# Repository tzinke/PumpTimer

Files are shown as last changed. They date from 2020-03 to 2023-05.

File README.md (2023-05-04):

<p>A timer for my pool pump using a Raspberry Pi Zero W and a custom-made PCB.</p>

# Pool Pump Timer Instructions

<p>This device emits its own wi-fi network which will allow you to connect to the controller and set schedules and toggle the pump on/off.</p>

<p>The name of the network is PumpController, and the password is PumpController2803Pool</p>
  
<p>This network is NOT connected to the internet, so you'll probably want to deselect auto-connect for this network (otherwise your device might automatically hop on this network and not be connected to the internet). To control the device, you will also need to turn cell data off if connecting with a phone.</p>

<p>Once connected, open a browser and navigate to pumpcontroller.com. This will pull up the controller interface.</p>

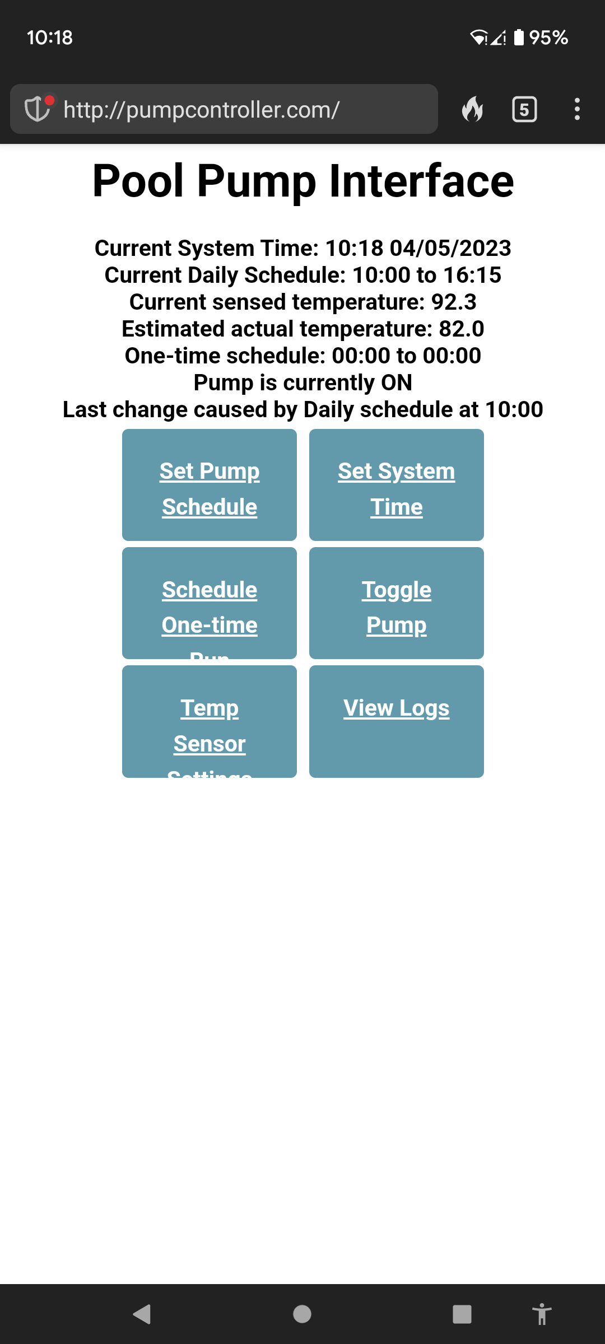
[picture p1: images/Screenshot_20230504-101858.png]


<p>Here, you can set a schedule to turn the pump on/off at the same time each day, set the on-board clock, set a "one-time run" (a schedule that will only execute a single time, after which the daily schedule will resume), toggle the pump on/off manually, and view logs from the last 3 months.
The on-board clock is very accurate with little drift, but it is not configured to automatically adjust for daylight savings.</p>

<p>The device is also configured to turn the pump on for at least 10 minutes if the temperature gets too close to 32F in order to prevent equipment damage from freezes.
The on-board temperature sensor isn't terribly accurate, so there is an adjustment factor that you can change to get it more accurate/modify the "freeze" threshold.</p>

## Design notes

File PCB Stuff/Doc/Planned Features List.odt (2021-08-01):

- 120VAC/60Hz to 5VDC converter
- Two relays – one for each phase of mains – with coils in parallel for simultaneous actuation
- Raspberry pi zero w as system controller
- Real-time clock w/ coin battery slot for accurate time keeping with or without main power
- Female headers for I2C, some GPIO for any future expansion (with pull-ups/impedance-matching resistors)
- Mounts to a raspberry pi zero w and to our old timer box (with 3D-printed mounting plate)

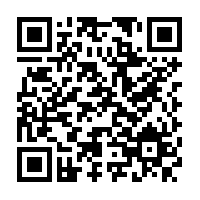
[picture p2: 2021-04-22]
images/medqr.png

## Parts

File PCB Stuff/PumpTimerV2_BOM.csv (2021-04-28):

Part | Value | Designator(s) | Count
RAC03-05SK | RAC03-05SK | PS1 | 1
ADW1205HLW | ADW1205HLW | K1 "K2" | 2
DMN67D7L | DMN67D7L | Q1 "Q2" | 2
BAV5004WS-7 | BAV5004WS-7 | D1 "D2" "D3" | 3
M20-9982046 | Conn_02x20_Odd_Even | J4 | 1
RX8900UA | RX8900UA | U1 | 1
CRGP0603F2K2 | 2k2 | R3 "R4" "R13" "R5" | 4
282856-2 | 282856-2 | J3 "J2" "J1" | 3
GMC31X5R107M10NT | 100u | C1 "C2" "C3" | 3
B4B-PH-SM4-TBT(LF)(SN) | B4B-PH-SM4-TBT(LF)(SN) | J6 | 1
ERJ-PA3J103V | 10k | R1 "R2" | 2
SML-D12U1WT86 | LED | D4 | 1
CRGCQ0603F330R | 330 | R14 | 1
50M025045G008 | 2.75mm | H1" "H3" "H5" "H6" "H4" "H2" | 6
TL3305AF160QG | TL3305AF160QG | SW1 | 1
LMK107BJ106MALTD | 10u | C4 | 1

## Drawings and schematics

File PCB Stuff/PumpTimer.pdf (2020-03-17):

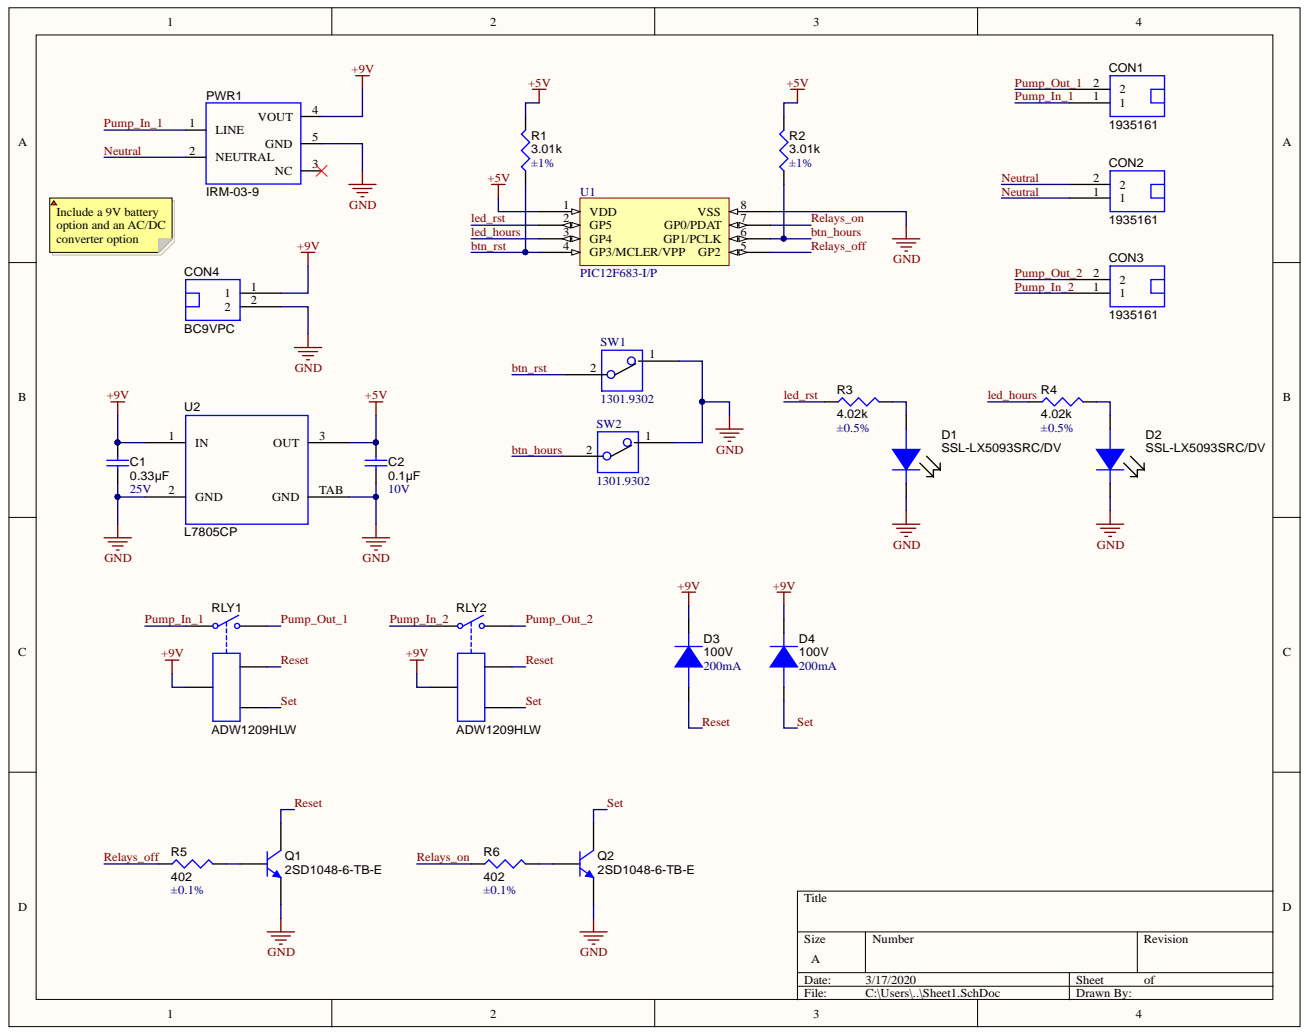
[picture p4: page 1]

Include a 9V battery
option and an AC/DC
converter option

GP5 2 GP4 3 | Relays_on

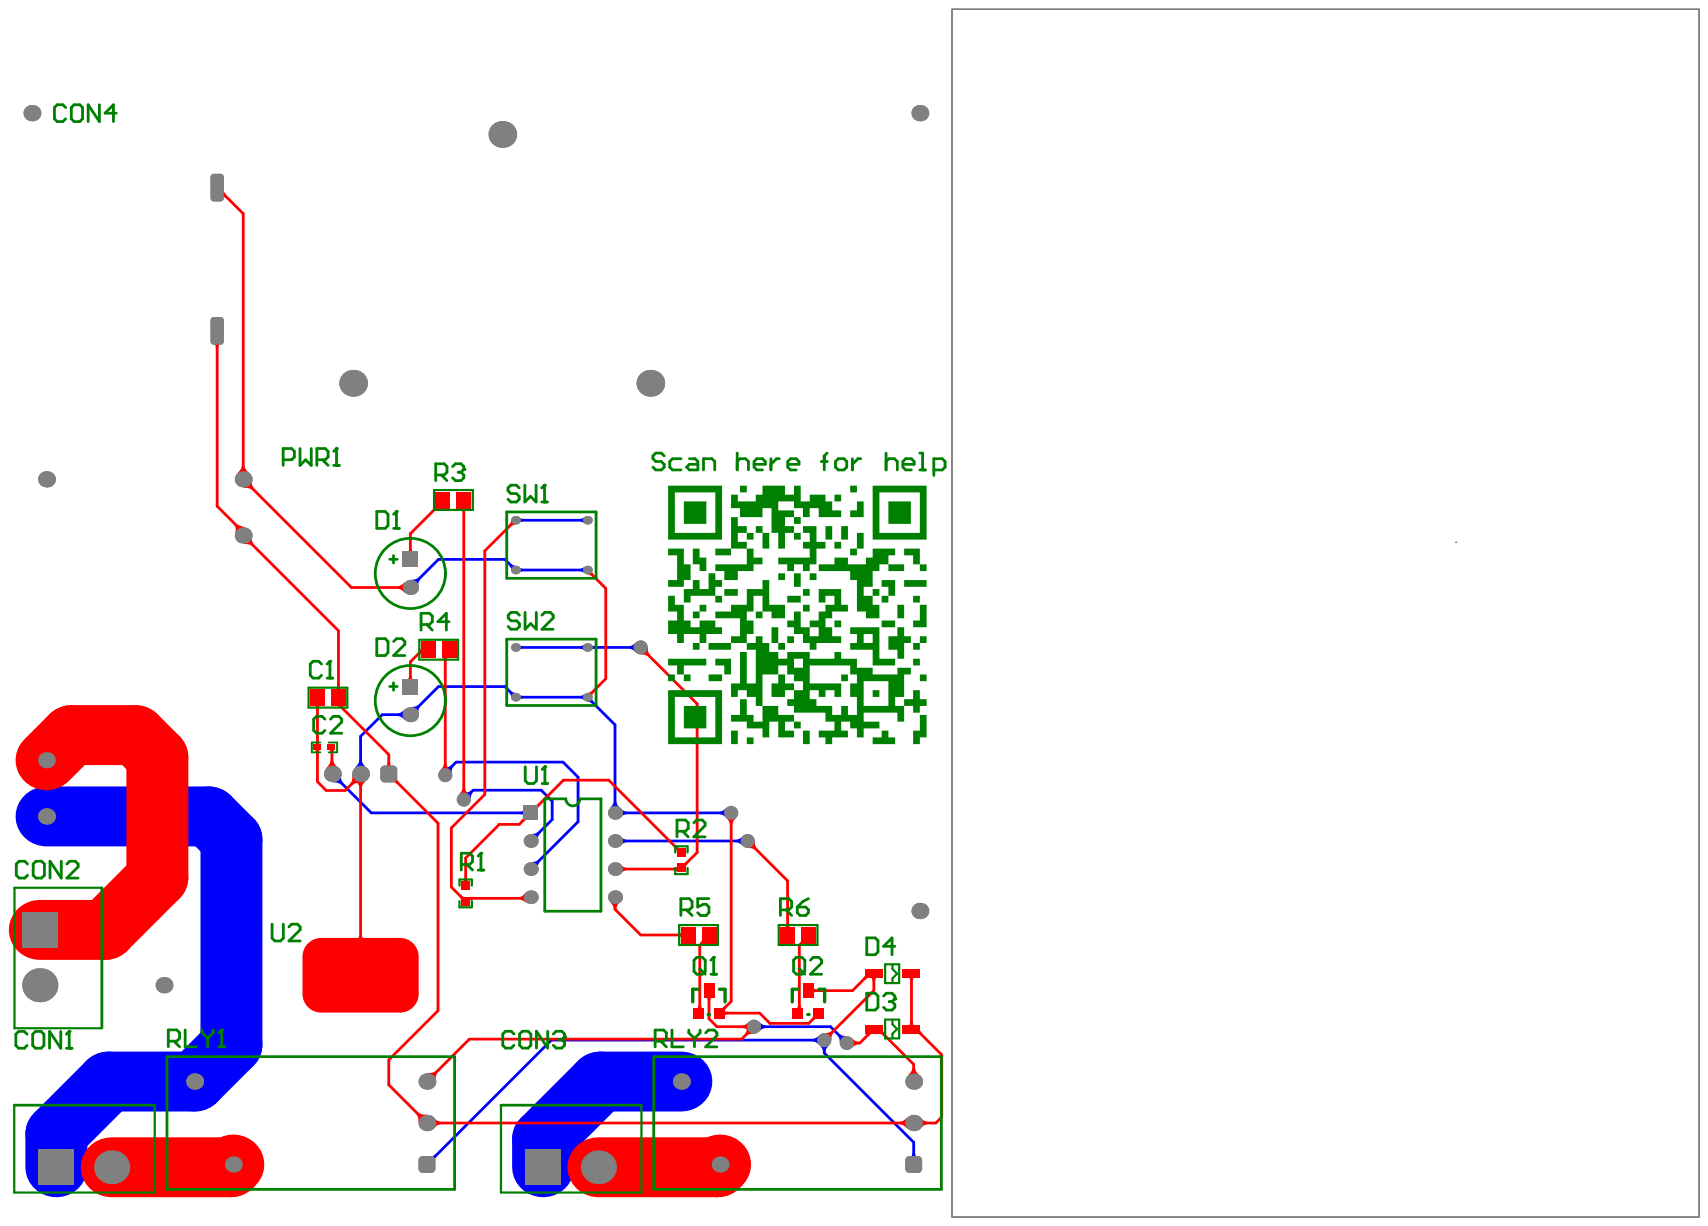
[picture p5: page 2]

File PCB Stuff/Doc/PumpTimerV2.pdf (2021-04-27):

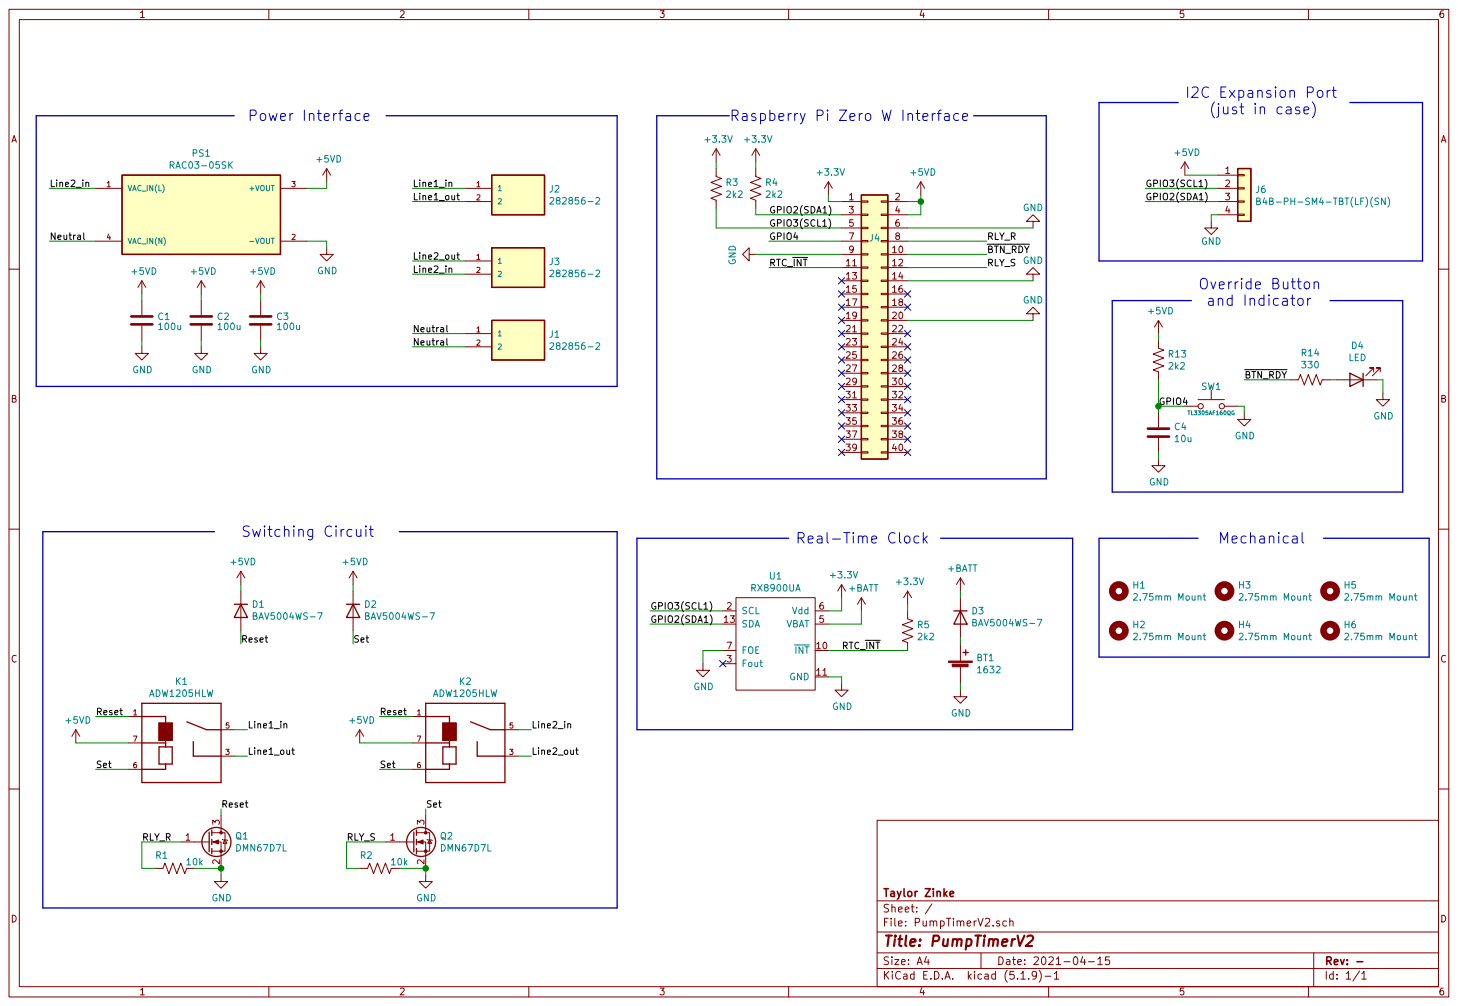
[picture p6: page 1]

J6B4B-PH-SM4-TBT(LF)(SN) GND

File: PumpTimerV2.sch Sheet: / Taylor Zinke GND

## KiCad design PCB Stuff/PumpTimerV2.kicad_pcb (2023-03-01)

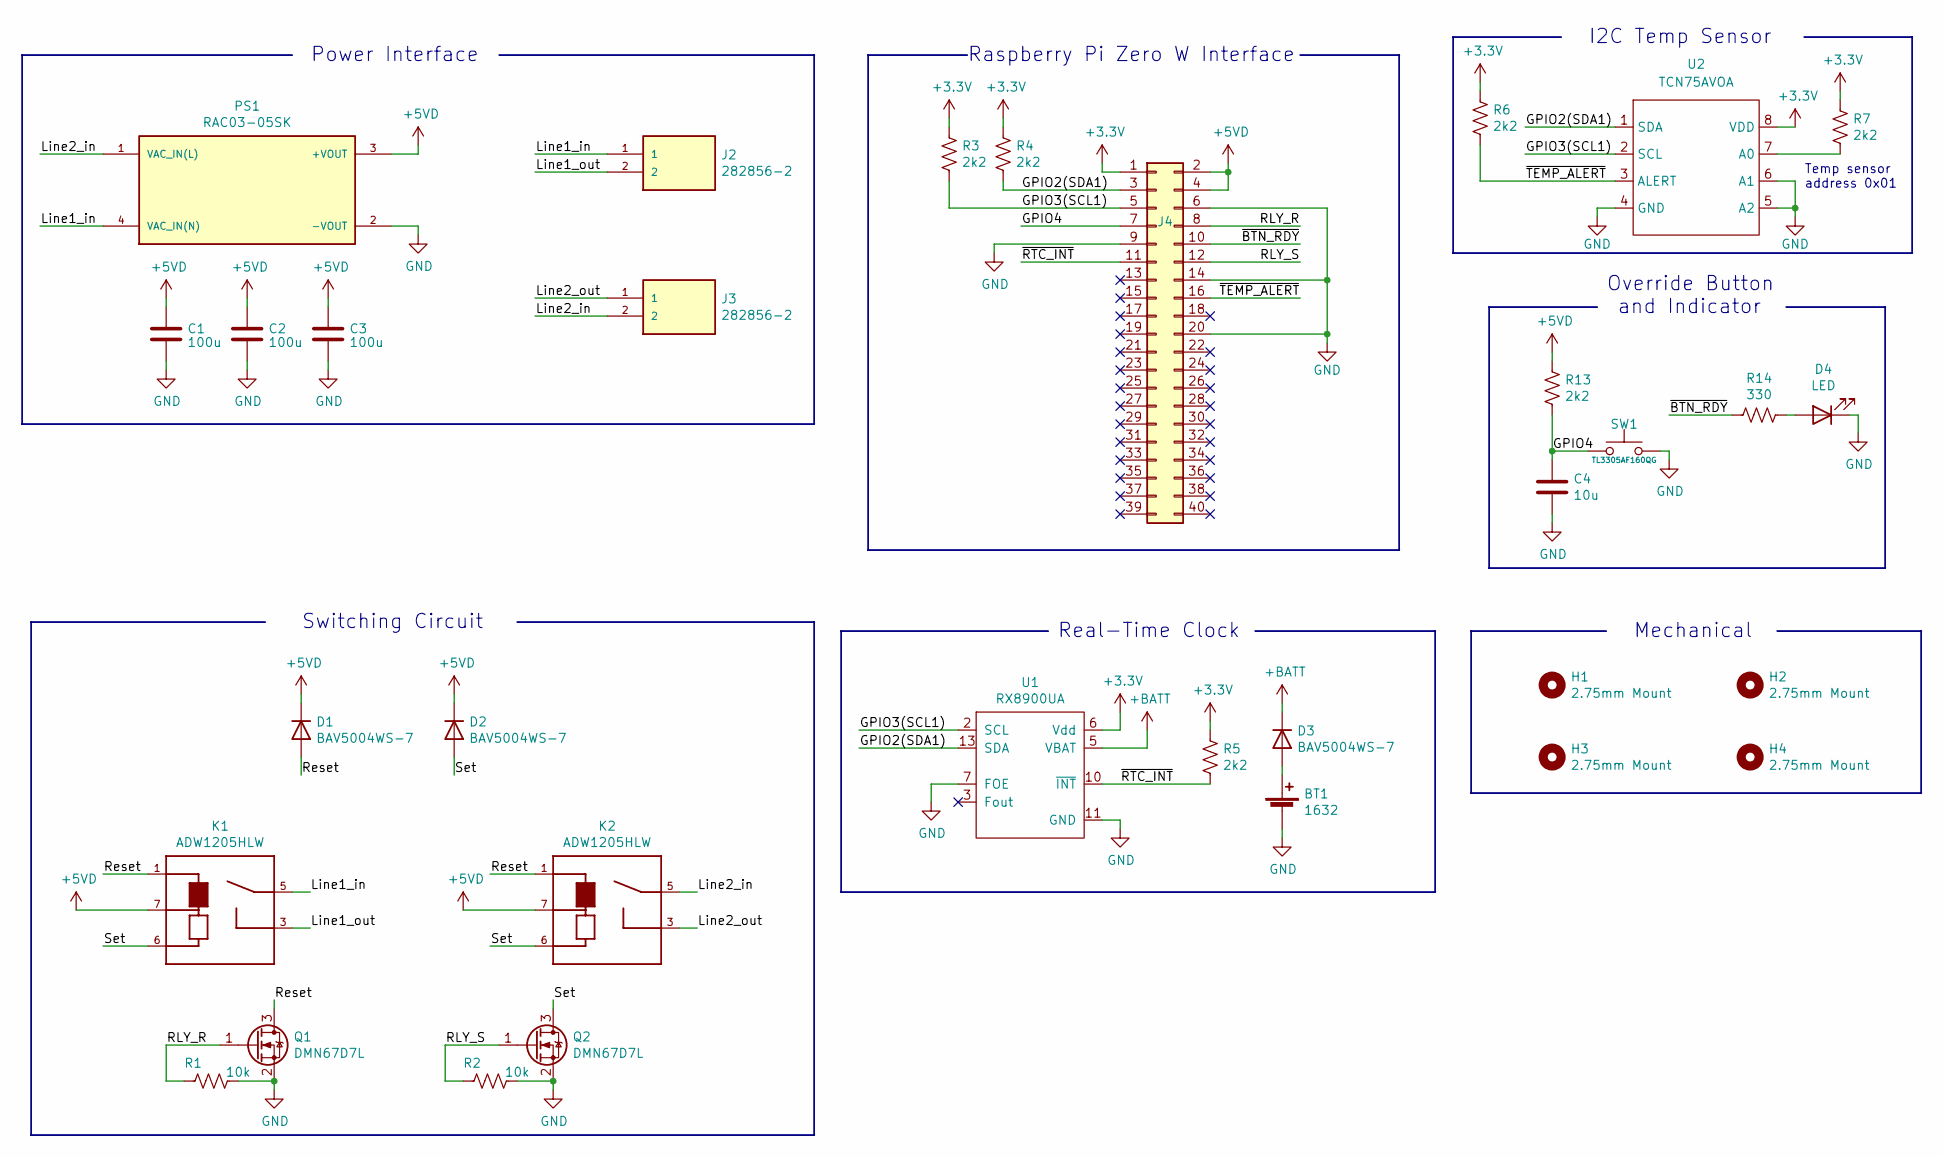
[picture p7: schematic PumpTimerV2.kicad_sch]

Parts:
BT1: 1632; Vertical_16mm_coin_holder; Part Keystone 1069
C1, C2, C3: 100u; C_1206_3216Metric_Pad1.33x1.80mm_HandSolder; Part GMC31X5R107M10NT
C4: 10u; C_0603_1608Metric_Pad1.08x0.95mm_HandSolder; Part LMK107BJ106MALTD
D1, D2, D3: BAV5004WS-7; D_SOD-323; Part BAV5004WS-7
D4: LED; LED_0603_1608Metric_Castellated; Part SML-D12U1WT86
H1, H2, H3, H4: 2.75mm Mount; MountingHole_2.7mm_M2.5; Part 50M025045G008
J2, J3: 282856-2; TE_282856-2; Part 282856-2
J4: Conn_02x20_Odd_Even; PinHeader_2x20_P2.54mm_Vertical; Part M20-9982046
K1, K2: ADW1205HLW; RELAY_ADW1205HLW; Part ADW1205HLW
PS1: RAC03-05SK; Part RAC03-05SK
Q1, Q2: DMN67D7L; SOT-23; Part DMN67D7L
R1, R2: 10k; R_0603_1608Metric_Pad0.98x0.95mm_HandSolder; Part ERJ-PA3J103V
R3, R4, R5, R6, R7, R13: 2k2; R_0603_1608Metric_Pad0.98x0.95mm_HandSolder; Part CRGP0603F2K2
R14: 330; R_0603_1608Metric_Pad0.98x0.95mm_HandSolder; Part CRGCQ0603F330R
SW1: TL3305AF160QG; Part TL3305AF160QG
U1: RX8900UA; SOP-14_127P780x200; Part RX8900UA
U2: TCN75AVOA; SOIC-8_3.9x4.9mm_P1.27mm

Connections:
+3V3: J4.1, R3.1, R4.1, R5.1, R6.1, R7.1, U1.6 (Vdd), U2.8 (VDD)
+5VD: C1.1, C2.1, C3.1, D1.2 (K), D2.2 (K), J4.2, J4.4, K1.7, K2.7, PS1.3 (+VOUT), R13.1
+BATT: D3.2 (K), U1.5 (VBAT)
/GPIO2(SDA1): J4.3, R4.2, U1.13 (SDA), U2.1 (SDA)
/GPIO3(SCL1): J4.5, R3.2, U1.2 (SCL), U2.2 (SCL)
/GPIO4: C4.1, J4.7, R13.2, SW1.1
/Line1_in: J2.1, K1.5, PS1.4 (VAC_IN(N))
/Line1_out: J2.2, K1.3
/Line2_in: J3.2, K2.5, PS1.1 (VAC_IN(L))
/Line2_out: J3.1, K2.3
/RLY_R: J4.8, Q1.1 (G), R1.2
/RLY_S: J4.12, Q2.1 (G), R2.2
/Reset: D1.1 (A), K1.1, K2.1, Q1.3 (D)
/Set: D2.1 (A), K1.6, K2.6, Q2.3 (D)
/~BTN_RDY: J4.10, R14.2
/~RTC_INT: J4.11, R5.2, U1.10 (~INT)
/~TEMP_ALERT: J4.16, R6.2, U2.3 (ALERT)
GND: BT1.NEG (-), C1.2, C2.2, C3.2, C4.2, D4.1 (K), J4.6, J4.9, J4.14, J4.20, PS1.2 (-VOUT), Q1.2 (S), Q2.2 (S), R1.1, R2.1, SW1.2, U1.7 (FOE), U1.11 (GND), U2.4 (GND), U2.5 (A2), U2.6 (A1)
unnamed: BT1.POS (+), D3.1 (A)
unnamed: D4.2 (A), R14.1
unnamed: R7.2, U2.7 (A0)

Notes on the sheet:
Override Button and Indicator
Mechanical
Switching Circuit
I2C Temp Sensor
Raspberry Pi Zero W Interface
Power Interface
Real-Time Clock
Temp sensor address 0x01

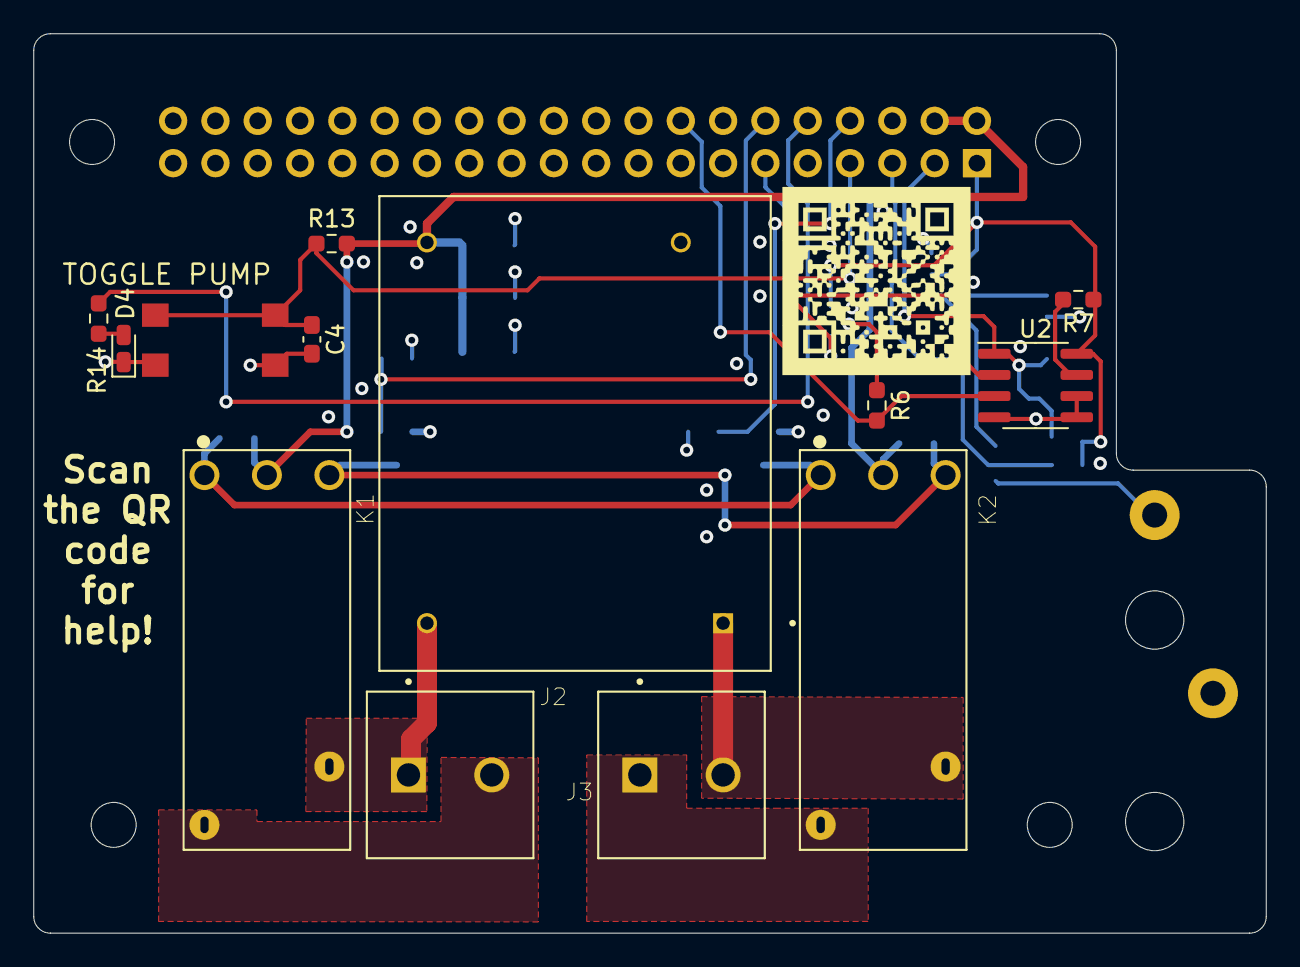
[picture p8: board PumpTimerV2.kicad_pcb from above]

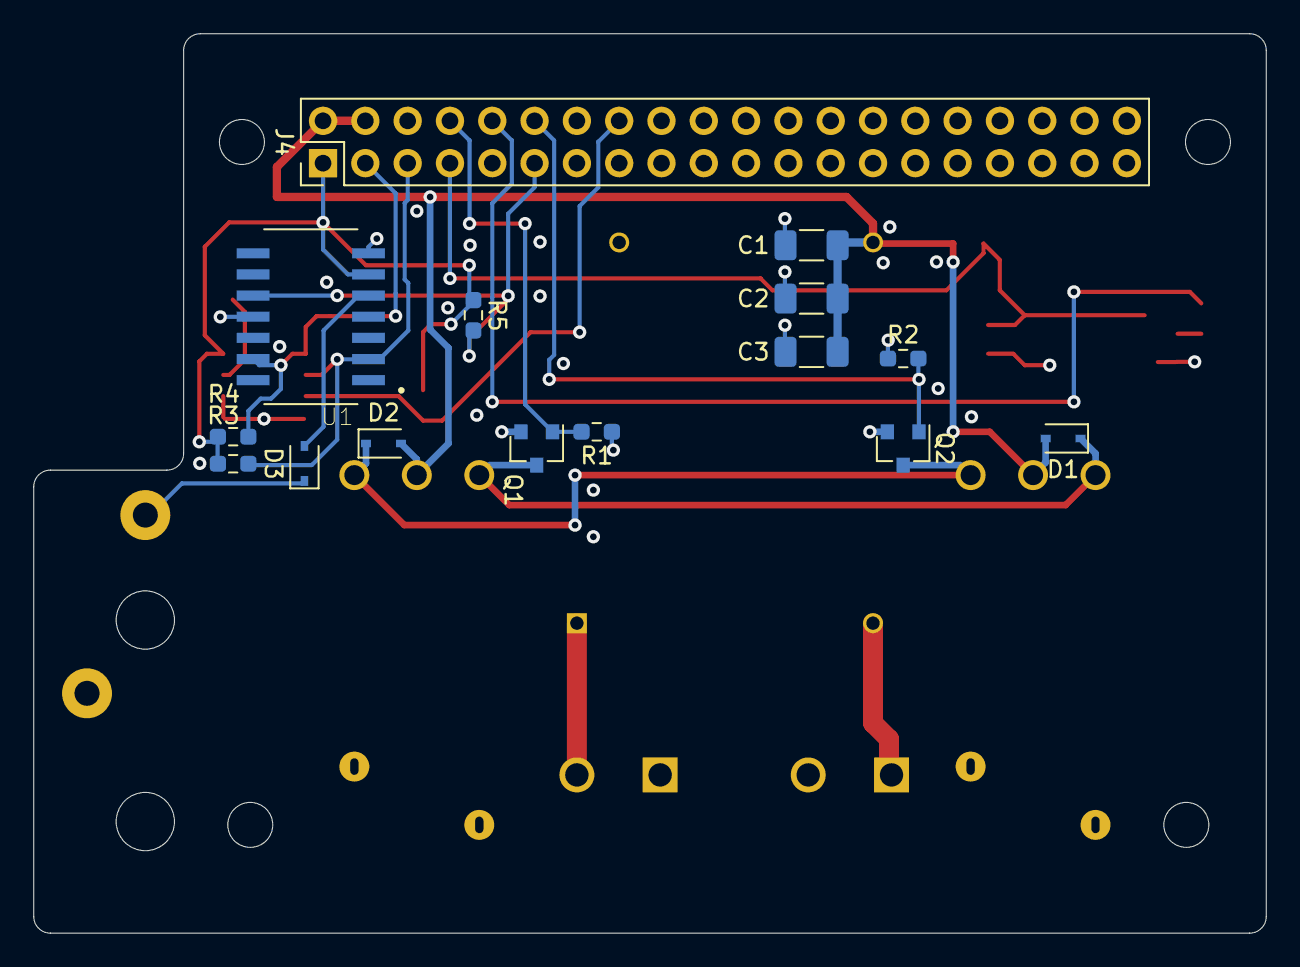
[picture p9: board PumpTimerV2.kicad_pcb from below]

Board: 4 copper layers, 74.0 x 54.0 mm, 33 parts (15 on the bottom side), 21 nets.

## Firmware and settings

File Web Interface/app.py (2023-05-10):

#!/usr/bin/python3

'''
app.py

Description
-----------
These functions are executed when requested by a client connected in a web browser to the address/port defined in this script.

Functions Defined
------------------
Function: top-level description
    Parameters
    Returns: Data type + description

set_schedule:

set_one_time:

set_time:

toggle_pump:

fetch_log:

Change Log
----------
27 Apr 2023 - Temp sensor operations added.

'''

##################################################################################################
# # Imports
##################################################################################################

import glob, os
import time
import smbus
import datetime
import subprocess
from flask import Flask, render_template, request, send_file
import RPi.GPIO as GPIO
from threading import Timer, Lock
from enum import Enum

##################################################################################################
# # Global Variables
##################################################################################################

# Define the address and port this server will run on
ip = "192.168.15.1"
server_port = 80

# Schedule and log file paths
# Schedule is written to file so the timer can resume
#   the schedule and temp offset (init data) in case of power outage
#   One-time schedules will be lost in power outage
initialization_data_path = "./static/initialization_data"
log_dir = "./static/logs/"
log_recovery = "./static/logRecovery"
log_path = '' # Will get set to current date
current_day = 0
class PumpState(Enum):
    DAILY_SCHED_ON = 1
    ONE_TIME_RUN_ON = 2
    WEB_TOGGLE_ON = 3
    BUTTON_ON = 4
    FREEZE_PROTECTION_ON = 5
    OFF = 6
class MonthNames(Enum):
    Jan = 1
    Feb = 2
    Mar = 3
    Apr = 4
    May = 5
    June = 6
    July = 7
    Aug = 8
    Sep = 9
    Oct = 10
    Nov = 11
    Dec = 12

# State variables
current_pump_state = PumpState.OFF
pump_one_time_run = False
lastEvent = "None" # Possible values: "button", "daily schedule", "one-time schedule", "pressure failure"
lastEventTime = 0
general_cooldown = 0 # This is to prevent overly-frequent pump-state changes. Each change will incur a 3s general_cooldown
freeze_protection_cooldown = False # This is to prevent overly-frequent pump-state changes. If the freeze-protection changes pump state, it will stay so for at least 10 minutes
mutex = Lock() # This is to prevent unwanted interactions between timer and button events
sensor_temp = 0
temp_offset = 0
adjusted_temp = 0
freeze_protection_threshold = 33.5
temp_sensor_failure = False

# Schedule variables
currtime = -1
sched_on = 0
sched_off = 0
one_time_on = 0
one_time_off = 0
# Don't want one-time-run settings to remain active after completing
one_time_run_pending = 0 #0 = not pending; 1 = pending

# I2C variables
bus = smbus.SMBus(1)
rtc_addr = 0x32
temp_sensor_addr = 0x49 #todo might need to shift left 1 bit

sensors = {
    1 : {'name' : 'Time', 'data' : 'None'},
    2 : {'name' : 'Temp', 'data' : 'None'}
}

app = Flask(__name__)

##################################################################################################
# # Function Definitions/Client Routing
##################################################################################################

def rtc_set(time_string):
    """
    Description
    -----------
    This function writes to the registers of the RTC

    Parameters
    ----------
    time_string: String with the current 24-hour time formatted as
        "yyyy mm dd HH MM SS"

    Returns
    -------
    None

    Examples
    --------

    Change Log
    ----------

    Notes
    -----
    """
    currtime = datetime.datetime.strptime(time_string, "%Y %m %d %H %M %S")
    yy = currtime.year - 2000

    second= (int(currtime.second /10) * 16) + (currtime.second % 10)
    minute = (int(currtime.minute /10) * 16) + (currtime.minute % 10)
    hour = (int(currtime.hour /10) * 16) + (currtime.hour % 10)
    day = (int(currtime.day /10) * 16) + (currtime.day % 10)
    month = (int(currtime.month /10) * 16) + (currtime.month % 10)
    year = (int(yy /10) * 16) + (yy % 10)

    bus.write_i2c_block_data(rtc_addr, 0, [second, minute, hour, 1, day, month, year])

def rtc_get():
    """
    Description
    -----------
    This function reads from the registers of the RTC and sets the system time
        accordingly.

    Parameters
    ----------
    None

    Returns
    -------
    A list containing the current RTC setting

    Examples
    --------

    Change Log
    ----------

    Notes
    -----
    """
    regs = bus.read_i2c_block_data(rtc_addr, 0, 7)

    seconds = "%d" % ((int(regs[0]/16) * 10) + (regs[0] % 16))
    if int(seconds) < 10:
        seconds = "0" + seconds
    minutes = "%d" % ((int(regs[1]/16) * 10) + (regs[1] % 16))
    if int(minutes) < 10:
         minutes = "0" + minutes
    hours = "%d" % ((int(regs[2]/16) * 10) + (regs[2] % 16))
    if int(hours) < 10:
         hours = "0" + hours
    day = "%d" % ((int(regs[4]/16) * 10) + (regs[4] % 16))
    if int(day) < 10:
         day = "0" + day
    month = "%d" % ((int(regs[5]/16) * 10) + (regs[5] % 16))
    if int(month) < 10:
         month = "0" + month
    year = "%d" % ((int(regs[6]/16) * 10) + (regs[6] % 16))
    if int(year) < 10:
         year = "0" + year

    return [seconds, minutes, hours, day, month, year]

def temp_get():
    bytes = bus.read_i2c_block_data(temp_sensor_addr, 0, 2)
    temp = int(bytes[0] << 8) + int(bytes[1])
    temp = float(temp * 0.00390625)
    return temp 

def updateLog():
    with open(log_path, 'a') as log:
        log.write("%s turned pump %s at %s\n" % (lastEvent, ("OFF" if (current_pump_state is PumpState.OFF) else "ON"), lastEventTime))
        log.write("Sensed temp: %7.1f\t, Adjusted temp: %7.1f\n" % (sensor_temp, adjusted_temp))

def startPump(source):
    global current_pump_state, general_cooldown
    if general_cooldown is 0:
        # GPIO18 high for 15ms
        GPIO.output(18, 1)
        time.sleep(0.015)
        GPIO.output(18, 0)
        current_pump_state = source
        print("Pump started by %s" % source.name)

        GPIO.output(15,1)
        general_cooldown = 1
        Timer(3, general_cooldown_counter, ()).start()

def stopPump():
    global current_pump_state, general_cooldown
    if general_cooldown is 0:
        # GPIO14 high for 15ms
        GPIO.output(14, 1)
        time.sleep(0.015)
        GPIO.output(14, 0)
        current_pump_state = PumpState.OFF

        GPIO.output(15,1)
        general_cooldown = 1
        Timer(3, general_cooldown_counter, ()).start()

def toggle_pump(button):
    global lastEvent, lastEventTime, mutex

    mutex.acquire()
    if (current_pump_state is PumpState.OFF):
        startPump(PumpState.BUTTON_ON)
    else:
        stopPump()

    mutex.release()
    lastEvent = "Button"
    lastEventTime = "%s:%s" % (sensors[0][2], sensors[0][1])
    updateLog()

def general_cooldown_counter():
    global general_cooldown
    general_cooldown = 0
    GPIO.output(15,0)
    
def freeze_protection_cooldown_counter():
    global freeze_protection_cooldown
    freeze_protection_cooldown = False

def application_tick():
    global mutex, sensors, lastEvent, lastEventTime, currtime, sensor_temp, adjusted_temp, one_time_on, one_time_off, one_time_run_pending, current_day, log_path, freeze_protection_cooldown
    # Check if the current time matches sched_on, sched_off, one_time_on, or one_time_off
    #   and change pump state if necessary
    sensors[0] = rtc_get()
    currtime = int(sensors[0][2])*100 + int(sensors[0][1])
    
    if not temp_sensor_failure:
        sensors[1] = temp_get()
        sensor_temp = (sensors[1] * 1.8) + 32.0 
        adjusted_temp = sensor_temp + temp_offset
        print("%7.1f + %7.1f = %7.1f" % (sensor_temp, temp_offset, adjusted_temp))

    drift_correction = 60 - int(sensors[0][0]) #Subtract out the seconds from timer delay so this happens on the minute
    print("Drift correction: %d" % drift_correction)

    mutex.acquire(blocking=False)
    if mutex.locked():
        if (adjusted_temp <= freeze_protection_threshold): # Risking freeze conditions!
            print("Freeze condition detected! PumpState is %s, freeze prot cooldown is %d" % (current_pump_state.name, freeze_protection_cooldown))
            if (current_pump_state is PumpState.OFF) and (freeze_protection_cooldown is False): # Pump is not on, and the cooldown period has ended
                print("In freeze protect block")
                startPump(PumpState.FREEZE_PROTECTION_ON)
                freeze_protection_cooldown = True
                Timer(10 * 60, freeze_protection_cooldown_counter, ()).start()
                lastEvent = "Freeze protection on"
                lastEventTime = "%s:%s" % (sensors[0][2], sensors[0][1])
                updateLog()

        else:
            desired_pump_state = current_pump_state
            lastEventBuffer = 0
            source = PumpState.OFF

            if (current_pump_state is PumpState.FREEZE_PROTECTION_ON) and (freeze_protection_cooldown is False): # Pump is on due to freeze protection, and the cooldown poweriod has ended
                desired_pump_state = 0 # Want to turn the pump off. Schedules can override this.
                lastEventBuffer = "Freeze protection off"

            # Check one-time schedule first to give preference to one-time schedules
            # Check off-times first so time-collisions will result in pump state OFF
            if one_time_run_pending is 1:
                if currtime == one_time_off:
                    desired_pump_state = 0
                    one_time_run_pending = 0 # one-time-run schedule finished
                    one_time_on = one_time_off = 0
                    lastEventBuffer = "One-time schedule"
                elif currtime == one_time_on:
                    desired_pump_state = 1
                    source = PumpState.ONE_TIME_RUN_ON
                    lastEventBuffer = "One-time schedule"
            else:
                if currtime == sched_off:
                    desired_pump_state = 0
                    lastEventBuffer = "Daily schedule"
                elif currtime == sched_on:
                    desired_pump_state = 1
                    source = PumpState.DAILY_SCHED_ON
                    lastEventBuffer = "Daily schedule"
                    
            if (desired_pump_state is 1) and (current_pump_state is PumpState.OFF):
                startPump(source)
                lastEvent = lastEventBuffer
                lastEventTime = "%s:%s" % (sensors[0][2], sensors[0][1])
                updateLog()
            elif (desired_pump_state is 0) and (not (current_pump_state is PumpState.OFF)):
                stopPump()
                lastEvent = lastEventBuffer
                lastEventTime = "%s:%s" % (sensors[0][2], sensors[0][1])
                updateLog()

        mutex.release()

    timer_clock = Timer(drift_correction, application_tick, ())
    timer_clock.start()

    if current_day is not int(sensors[0][3]):
        current_day = int(sensors[0][3])
        log_path = "%s%s_%s_%s" % (log_dir, sensors[0][3], sensors[0][4], sensors[0][5])

        with open(log_path, 'a') as newlog:
            newlog.write("Starting log at %s\n" % currtime)
        with open(log_recovery, 'w') as newlogrec:
            newlogrec.write("%d\n" % current_day)
            newlogrec.write(log_path)

        try:
            # Delete log from 3 months ago to remove clutter (who needs such an old log?)
            month = int(sensors[0][4])
            if month < 4:
                for f in glob.glob("%s%s_%02d*" % (log_dir, sensors[0][3], 9 + month)):
                    print("Attempting to remove log %s" % f)
                    os.remove(f)
            else:
                for f in glob.glob("%s%s_%02d*" % (log_dir, sensors[0][3], month - 3)):
                    print("Attempting to remove log %s" % f)
                    os.remove(f)
        except OSError: # Such log doesn't exist
            print("Failed to remove log!")
            pass

@app.route("/")
def main():
    """
    Description
    -----------
    This function gets called when the client navigates to "[serveraddress]/"
    (AKA the home page of the web app)

     Parameters
    ----------
    None

    Returns
    -------
    Renders the main.html page

    Examples
    --------

    Change Log
    ----------

    Notes
    -----
    """
    templateData = {
        'curr_time' : ("%s:%s %s %s 20%s" %  (sensors[0][2], sensors[0][1], sensors[0][3], MonthNames(int(sensors[0][4])).name, sensors[0][5])),
        'sensed_temp' : ("%4.1f" % sensor_temp),
        'estimated_temp' : ("%4.1f" % adjusted_temp),
        'sched_on' : ("%02d:%02d" % (int(sched_on/100), sched_on - (int(sched_on/100) * 100))),
        'sched_off' : ("%02d:%02d" % (int(sched_off/100), sched_off - (int(sched_off/100) * 100))),
        'once_on' : ("%02d:%02d" % (int(one_time_on/100), one_time_on - (int(one_time_on/100) * 100))),
        'once_off' : ("%02d:%02d" % (int(one_time_off/100), one_time_off - (int(one_time_off/100) * 100))),
        'last' : lastEvent,
        'lastEventTime' : lastEventTime,
        'pump_state' : ("Pump is currently OFF" if (current_pump_state is PumpState.OFF) else "Pump is currently ON")
    }
    # Pass the template data into the template main.html and return it to the user
    return render_template('main.html', **templateData)

@app.route("/setSchedule", methods=['GET', 'POST'])
def set_schedule():
    global sched_off, sched_on, lastEvent, lastEventTime
    if request.method == 'POST':
        on_time = request.form['new_on']

        if not on_time == '':
            strsplt = on_time.split(':')
            on_hh = int(strsplt[0])
            on_mm = int(strsplt[1])

            if (23 < on_hh) or (0 > on_hh):
                raise TypeError("HOUR: You must enter an integer between 0 and 23")
            elif(59 < on_mm) or (0 > on_mm):
                raise TypeError("MINUTE: You must enter an integer between 0 and 59")

            sched_on = (on_hh * 100) + on_mm

            with open(initialization_data_path, "r") as file:
                file.readline()
                old_off = int(file.readline())

            with open(initialization_data_path, "w") as file:
                file.write("%d\n" % sched_on)
                file.write("%d\n" % old_off)
                file.write("%5.1f\n" % temp_offset)
                file.write("%7.1f" % freeze_protection_threshold)

        off_time = request.form['new_off']

        if not off_time == '':
            strsplt = off_time.split(':')
            off_hh = int(strsplt[0])
            off_mm = int(strsplt[1])

            if (23 < off_hh) or (0 > off_hh):
                raise TypeError("HOUR: You must enter an integer between 0 and 23")
            elif(59 < off_mm) or (0 > off_mm):
                raise TypeError("MINUTE: You must enter an integer between 0 and 59")

            sched_off = (off_hh * 100) + off_mm

            with open(initialization_data_path, "r") as file:
                old_on = int(file.readline())

            with open(initialization_data_path, "w") as file:
                file.write("%d\n" % old_on)
                file.write("%d\n" % sched_off)
                file.write("%5.1f\n" % temp_offset)
                file.write("%7.1f" % freeze_protection_threshold)

        if (one_time_run_pending is 0):
            if sched_off < sched_on: # Wrap through midnight
                if (currtime >= sched_on) or (currtime < sched_off):
                    startPump(PumpState.DAILY_SCHED_ON)
                    print("Currtime >= sch on OR < sched_off -> pump on")
                    lastEvent = "Daily schedule"
                    lastEventTime = "%s:%s" % (sensors[0][2], sensors[0][1])
                    updateLog()
                elif not (current_pump_state is PumpState.OFF): # Outside new schedule time + pump is on
                    stopPump()
                    print("NOT currtime >= sch on OR < sched_off -> pump off")
                    lastEvent = "Daily schedule"
                    lastEventTime = "%s:%s" % (sensors[0][2], sensors[0][1])
                    updateLog()
            elif sched_off > sched_on:
                if (currtime >= sched_on) and (currtime < sched_off):
                    startPump(PumpState.DAILY_SCHED_ON)
                    print("Currtime >= sch on AND < sched_off -> pump on")
                    lastEvent = "Daily schedule"
                    lastEventTime = "%s:%s" % (sensors[0][2], sensors[0][1])
                    updateLog()
                elif not (current_pump_state is PumpState.OFF): # Outside new schedule time + pump is on
                    stopPump()
                    print("NOT currtime >= sch on AND < sched_off -> pump off")
                    lastEvent = "Daily schedule"
                    lastEventTime = "%s:%s" % (sensors[0][2], sensors[0][1])
                    updateLog()
            else: # sched_off is the same as sched_on
                lastEvent = "Daily schedule"
                lastEventTime = "%s:%s" % (sensors[0][2], sensors[0][1])
                stopPump()
                updateLog()

    templateData = {
        'curr_time' : ("%s:%s %s %s 20%s" %  (sensors[0][2], sensors[0][1], sensors[0][3], MonthNames(int(sensors[0][4])).name, sensors[0][5])),
        'curr_on' : ("%02d:%02d" % (int(sched_on/100), sched_on - (int(sched_on/100) * 100))),
        'curr_off' : ("%02d:%02d" % (int(sched_off/100), sched_off - (int(sched_off/100) * 100)))
    }

    return render_template('setSchedule.html', **templateData)

@app.route("/setOneTime", methods=['GET', 'POST'])
def set_one_time_run():
    global one_time_off, one_time_on, one_time_run_pending, lastEvent, lastEventTime
    if request.method == 'POST':
        try:
            strsplt = request.form['new_on'].split(':')
            on_hh = int(strsplt[0])
            on_mm = int(strsplt[1])

            strsplt = request.form['new_off'].split(':')
            off_hh = int(strsplt[0])
            off_mm = int(strsplt[1])

            if (23 < on_hh) or (23 < off_hh) or (0 > on_hh) or (0 > off_hh):
                raise TypeError("HOUR: You must enter an integer between 0 and 23")
            elif(59 < on_mm) or (59 < off_mm) or (0 > on_mm) or (0 > off_mm):
                raise TypeError("MINUTE: You must enter an integer between 0 and 59")

            one_time_on = (on_hh * 100) + on_mm
            one_time_off = (off_hh * 100) + off_mm

            print("Got one-time on:\t%d\nOne-time off:\t%d\n" % (one_time_on, one_time_off))

            one_time_run_pending = 1
            if one_time_off < one_time_on: # Wrap through midnight
                if (currtime >= one_time_on) or (currtime < one_time_off):
                    startPump(PumpState.ON_TIME_RUN_ON)
                    print("One-time schedule includes current time. Turning pump on\n")
                    lastEvent = "One-time schedule"
                    lastEventTime = "%s:%s" % (sensors[0][2], sensors[0][1])
                    updateLog()
                elif not (current_pump_state is PumpState.OFF):
                    stopPump()
                    print("Pump was on outside of new one-time schedule. Turning pump off\n")
                    lastEvent = "One-time schedule"
                    lastEventTime = "%s:%s" % (sensors[0][2], sensors[0][1])
                    updateLog()
            elif one_time_off > one_time_on:
                if (currtime >= one_time_on) and (currtime < one_time_off):
                    startPump(PumpState.ONE_TIME_RUN_ON)
                    print("One-time schedule includes current time. Turning pump on\n")
                    lastEvent = "One-time schedule"
                    lastEventTime = "%s:%s" % (sensors[0][2], sensors[0][1])
                    updateLog()
                elif not (current_pump_state is PumpState.OFF):
                    stopPump()
                    print("Pump was on outside of new one-time schedule. Turning pump off\n")
                    lastEvent = "One-time schedule"
                    lastEventTime = "%s:%s" % (sensors[0][2], sensors[0][1])
                    updateLog()
            elif one_time_on == one_time_off:
                one_time_on, one_time_off, one_time_run_pending = 0, 0, 0
        except: # One of the times entered was not a valid integer
            one_time_on = 0
            one_time_off = 0

    templateData = {
        'curr_on' : ("%02d:%02d" % (int(one_time_on/100), one_time_on - (int(one_time_on/100) * 100))),
        'curr_off' : ("%02d:%02d" % (int(one_time_off/100), one_time_off - (int(one_time_off/100) * 100))),
        'curr_time' : ("%s:%s %s %s 20%s" %  (sensors[0][2], sensors[0][1], sensors[0][3], MonthNames(int(sensors[0][4])).name, sensors[0][5])),
    }

    return render_template('setOneTime.html', **templateData)
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

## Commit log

2020-03-17 Uploading 3D PCB and schematic/2D PCB
2020-03-17 Created PCB Stuff folder
2020-03-17 Adding PCB PDFs. Download PCB1.pdf to view
2020-03-17 3D PCB model. Use Acrobat Reader to view.
2020-03-17 PCB and electrical schematic
2020-03-17 Fixed microcontroller pins in schematic
2020-03-17 Fixed pin numbers, increased relay actuation timing
2020-03-19 Changed pump's run-time pattern
    Previous version had pump's run-time dispersed symmetrically over 24 hours. I read online that running the pump at night isn't very useful, so this version runs the pump evenly over 12 hours (aimed a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
2020-04-07 Code clean-up, reenabling interrupts after disable
    Forgot to re-enable the interrupts once they had been disabled by a short-press of rst button.
2020-04-12 Added pictures of buttons
2020-04-16 Added drift correction, removed on-off-on pattern
    I'm not convinced the pattern made sense. Seems like shifting the run-time back in the day and having it run without discontinuity would leave the least amount of heat + direct sun in the pool, thus least amount of algae.
2020-06-12 Re-defined button functions and timer-overriding
2020-07-13 Fixed some logic errors
    Timed pump state was only being set if the timer wasn't overridden in the increment/decrement functions. It should be set regardless. It was also only being set in the checktime function if in an override state.
2021-04-13 Adding KiCad documents
    [PumpTimerV2.kicad_pcb, PumpTimerV2.sch]
2021-04-14 Adding button interface + LED indicator for manual switching of pump state
    [PumpTimerV2.kicad_pcb, PumpTimerV2.sch]
2021-04-15 Beginning layout. Removed a few non-critical components that will not fit.
    [PumpTimerV2.kicad_pcb, PumpTimerV2.sch]
2021-04-15 Temoprarily adding 3D models, removing stuff in PCB layout
    [BatteryHolder-3030.step, PumpTimerV2.kicad_pcb]
2021-04-15 Same as last. Need to flip RPI and connector. Line up for mounting.
    [PumpTimerV2.kicad_pcb, PumpTimerV2.sch]
2021-04-15 Clean-up, changing board size + adding bigger header for rpi
    [BatteryHolder-3030.step, PumpTimerV2.kicad_pcb, PumpTimerV2.sch]
2021-04-19 Work on PCB layout
    [PumpTimerV2.kicad_pcb]
2021-04-20 Start routing
    [PumpTimerV2.kicad_pcb]
2021-04-21 Routing and placement
    [PumpTimerV2.kicad_pcb, PumpTimerV2.sch]
2021-04-21 Finished placement and routing. Everything needs reviewed.
    [PumpTimerV2.kicad_pcb]
2021-04-21 Moving battery holder onto tab. Need to add mounting holes at bottom of board and review.
    [PumpTimerV2.kicad_pcb]
2021-04-22 Adding QR code
    [PumpTimerV2.kicad_pcb]
2021-04-22 Slight rearranging, changing neutral screw terminal to higher-current model
    [PumpTimerV2.kicad_pcb, PumpTimerV2.sch]
2021-04-23 Raspberry Pi header was backwards... Needs rerouted.
    [PumpTimerV2.kicad_pcb]
2021-04-23 Started re-routing after flipping rpi header
    [PumpTimerV2.kicad_pcb]
2021-04-23 Making sure schematic and PCB match. Finished re-routing after flipping rpi header.
    [PumpTimerV2.kicad_pcb, PumpTimerV2.sch]
2021-04-24 Potentially final routing & review. Might check things over one more time before submitting for fab
    [PumpTimerV2.kicad_pcb, PumpTimerV2.sch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]
2021-04-26 Moving things around to have bigger traces on the AC lines
    [PumpTimerV2.kicad_pcb]
2021-04-27 Finished routing bigger AC-line traces
    [PumpTimerV2.kicad_pcb, PumpTimerV2.sch]
2021-04-28 Adding BOM
    [PumpTimerV2.kicad_pcb, PumpTimerV2.sch, PumpTimerV2_BOM.csv]
2021-05-17 Adding mounting plate (maybe shouldn't be part of the main project since it's specific to my enclosure)
    [mount plate.FCStd]
2021-06-14 Changing "mutex" behavior for button function
2021-06-15 Adding drift correction for PT task, commenting out PT stuff until it's installed into system
    [app.py]
2021-06-17 Fixing scheduling functions, rtc_set(), error handling, changed timer task function
    [app.py]
2021-06-21 Fixed rtc function calls.
    [app.py]
2021-06-21 Fixing syntax errors, incorrect css link
    [app.py]
2021-06-22 Adding css file, moving rtc functions into app.py, adding setSchedule, custom buttons in html pages
2021-06-23 Fixing current time displayed on pages, minor bugs
    [app.py]
2021-06-23 Fixing schedule behaviors for schedule change, system time change, and system boot
    [app.py]
2021-07-06 Adding a TODO so I don't forget to switch to a true mutex
2021-07-23 Various fixes. Improving schedule logic, html issues.
    [app.py]
2021-07-24 Switching mutex to threading.Lock
2021-07-31 Fixed issue with one-time-run setting. Need to test setting a new one-time schedule when the pump is on outside of said schedule
    [app.py]
2021-08-01 Fixing info on main page. Attempting to fix /toggle bug, but it's still giving errors. Need to return main.html when user navigates to /toggle
    [app.py]
2021-08-01 Added event logging. Tried fixing event-time reporting for /main. Tried fixing /toggle.
    [app.py]
2021-08-03 Fixed syntax error, log_path wasn't declared global in checkTime
    [app.py]
2021-08-15 appToggle() was throwing an error without a return statement. Copied main()'s code into appToggle()
    [app.py]
2021-10-13 Using the web toggle button will now redirect to / instead of leaving /toggle in the address bar.
2023-02-16 Removed "Neutral" net (my AC/DC converter died. Seems like 230V input is nominal anyways)
    [PumpTimerV2.kicad_pcb, PumpTimerV2.kicad_sch, PumpTimerV2.sch]
2023-02-16 Added temp sensor. Started adding to PCB but not yet placed or routed.
    [PumpTimerV2.kicad_pcb, PumpTimerV2.kicad_sch]
2023-03-01 Rerouted PCB with temp sensor in place
    [PumpTimerV2-B_Cu.gbl, PumpTimerV2-B_Fab.gbr, PumpTimerV2-B_Mask.gbs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]
2023-03-13 Fixed page width on mobile
    [app.py]
2023-04-27 Added temp sensor operations
    [PumpTimerV2.kicad_sch]
2023-05-01 Update pump state logic
2023-05-02 Fixed some issues found while testing freeze protection. Fixed log deletion.
    [app.py]
2023-05-02 Added page to change temp sensor settings
2023-05-04 Made current date easier to read
2023-05-10 Fixed a few issues in web toggle callback
    [app.py]
